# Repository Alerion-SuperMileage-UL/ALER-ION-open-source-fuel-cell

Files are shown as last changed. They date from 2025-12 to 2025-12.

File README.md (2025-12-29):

# ALÉR-ION OPEN SOURCE HYDROGEN FUEL CELL
*Feel free to contact me at mederic.chalifour.1@ulaval.ca for any questions.*

Alérion Supermileage is a student group at l'Université Laval who focuses on the development of high efficiency vehicles for various competitions. Up until 2024, the team always relied on internal combustion engines. They then transitioned toward an electric-driven system with a battery. In 2025, the project of a self-made hydrogen PEM fuel cell was born. With the spirit of sharing knowledge and helping others develop this technology, all the relevant design files are released as an open-source project.

This is a PEM open cathode fuel cell which turns pure (or prehumidified) hydrogen gas into electrical power.

**DISCLAIMER: At the moment of writing this, the prototype still has reliability issues. This stack is prone to leaking. Alérion Supermileage and every contributors of this project waive all responsibility related to the usage of this fuel cell design. Note that hydrogen is a flammable gas. Use these files at your own risk.**

{F411903D-C956-4F15-B26A-56FD519BAC25}



# Stack general design
This project was realized as a "Projet de fin d'étude" and the final design report is available (in French) in [Additional documentation/Rapport_final_PFE.pdf](https://github.com/Alerion-SuperMileage-UL/ALER-ION-open-source-fuel-cell/blob/f2cdef219edfe725619d7147de9b8b1a14c1f4f9/Additional%20documentation/Rapport_final_PFE.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). 

The aimed power rating of this fuel cell is ~300 W. Some PEM fuel cells can reach a power density of 0.6 W/cm², so the total active surface area needs to be at least 500 cm². Next, the maximum voltage allowed in this project was 60V. With the assumption that the maximum voltage per cell, would be ~1 V in operation, the stack would require ~60 cells of 8.3 cm² of active area. This figure was rounded up to a square of 3 cm × 3 cm (9 cm²) to optimize the cutting of the 30cm x 30cm electrode sheets. Note that the 60 cells can be distributed in more than one stack connected in series to facilitate the assembly and maintenance.

# CAD files
The CAD files for this project are available in [CAD files](https://github.com/Alerion-SuperMileage-UL/ALER-ION-open-source-fuel-cell/tree/main/CAD%20files). All files are available in *.step* format and as fusion 360 files (with the history tree for easy modification).

The `Fuel cell stack assembly` file is the CAD file of the whole fuel cell stack.

# Bill of materials
The bill of materials is available in [BOM/BOM.xlsx](https://github.com/Alerion-SuperMileage-UL/ALER-ION-open-source-fuel-cell/tree/main/BOM).

# Membrane Electrode Assembly (MEA)

The MEA is composed of two carbon cloth electrodes sandwiched around a proton-exchange membrane.

{682CDC34-29BD-45FB-BDDA-95B5D1C561A5}

  ## Proton exchange membrane
  The proton exchange membrane used was a [HP9-Pt ePTFE Reinforced, Pt Impregnated PFSA Membrane](https://www.fuelcellstore.com/eptfe-reinforced-pfsa-membrane-9-microns-pt-impregnated?search=78010010) from the [Fuel Cell store](www.fuelcellstore.com).

**Note:** 

* The membrane is shipped with a plastic cover film on one side. This film is useful to hold the membrane flat during the cutting and hot pressing steps, but should be removed before the stack assembly.
* Being only 9 µm thick, this membrane was selected aiming for high performance. However, even though it could handle the working pressure (~6 psi) when tested in a single cell stack, it was shown to be a weak point when scaling up to multiple cells. It seems to be easily punctured or torn, either in the manual assembly process or by the hydrogen pressure.
* " [...] *This membrane has a cover film on one face in order to protect the membrane during shipping.  Platinum impregnation is done on the face that is away from the cover film. For best utilization of the Pt impregnation from the membrane manufacturer, it is recommended that the Pt side is placed toward the anode of the electrolyzer cell (cathode of the fuel cell) electrochemical cell.  This Pt impregnation is actually a Pt nanopowder that is incorporated into the entire surface of the membrane on the side opposite the single backing.  This platinum layer is not sufficient to sustain the electrochemical reactions of the cells, it is only intended to react the minute crossover gases that occur naturally in all membranes.* [...]" 

**Recommendation:** For future development, it might be wiser to start using a thickness closer to the industry standard of 50 µm to obtain a reliable stack, and then go down in thickness to optimise the performance.

  ### Automated cutting
  In order to cut each membrane precisely and reliably, an *Ender 3* 3D printer was converted to a CNC drag knife using a "plotter blade". During this process, the membrane was left on its protective plastic film.

**Close up picture of the cutting process:**



### Membrane CAD file
The CAD file for the membrane can be found in [CAD files/Membrane](https://github.com/Alerion-SuperMileage-UL/ALER-ION-open-source-fuel-cell/tree/main/CAD%20files/Membrane).

  ## Electrode

The electrode selected for this project was the [2 mg/cm² Platinum Black - Carbon Cloth Electrode (W1S1011)](https://www.fuelcellstore.com/carbon-cloth-2-ptb-gas-diffusion-electrode-w1s1011?search=11060067) from the [Fuel Cell store](www.fuelcellstore.com). They were cut in 30mm X 30mm using a utility knife.

**Note and recommendation:** A high platinum loading of 2 mg/cm² was selected aiming for high performance. This choice inflates the cost of the stack by a lot and a lower platinum loading (0.5 mg/cm² for example) could be used to reduce the testing and development cost. Also note that the carbon cloth electrode, which was selected for being easier to work with compared to carbon paper electrode, is better suited at high humidity level [(Wang, 2007)](https://doi.org/10.1016/j.electacta.2006.11.012).

  ## Hot press
To make each MEA, the precut membrane is hot pressed between two precut electrodes. The heated press used in this project is a *5 Ton Portable Hydraulic Heat Press Machine 2.3 x 4.7 Inch*.



For each MEA, a printed template and some tape were used to align the electrode to the membrane. The membrane was left on its plastic protective film during the pressing but the bottom electrode was inserted between the membrane and the film by lifting the corner with some tweezers (beware not to scratch the membrane). Note that the platinum coating of the electrodes must face the membrane. 

Each MEA was hot pressed at 66 kg/cm², 97°C for 3.56 minutes to optimize the stack's performances [(Okur, 2013)](https://doi.org/https://doi.org/10.1016/j.energy.2013.05.001). The pressure was set suspending a weight on the press lever (accounting for the hydraulic mechanical advantage) and considering the area of the electrodes only (9 cm²).

# Graphite flow plates
The flow plates (bipolar plates), were made of 0.125" thick [Fully Resin Impregnated Graphite Plates](https://www.fuelcellstore.com/impervious-bipolar-graphite-plates). 
  ## Machining
  Each Plate were manufactured using a small benchtop CNC router (_Genmitsu CNC 3018-PRO_) with a 1/32" endmill.

**Note:** 
* Machining graphite produces a very fine dust. This should be done in a well ventilated area with appropriate respirators. A shop-vac was used to further control the produced dust.

  ## Flow field design and geometry
    Multiple flow fields geometry were tried and the ones producing the most power were selected. However, it should be noted that there was a high degree of uncertainty on the results so this process should be done again in the future.
    ### Hydrogen side (anode)
  Among others, the following flow fields were tried on the anode side:

IMG_5936 (1)

  The simple serpentine flow field was selected.
  
{30DB0875-6CFB-4B4F-8EC1-B9351816C968}

### Air side (cathode)

  All cathode flow fields that were tried followed the same idea of straight channels. The selection process was done before the optimisation of the gasket system. Indeed, nickel strips were added as back support for the gasket. The initial design was thus one that allowed the first PTFE gasket to self support and wasn't necessarily the most efficient one.

  {ACC28917-BCA8-4B8C-A650-7DEC884F8421}

  **Note:** 
  * The cathode design should be a balance between the conductivity (more graphite in contact with the electrode) and air availability (less graphite in contact with the electrode)
  * The depth of the channels also affects the strength of the plates. This should also be considered as cracked plates cause leakage.
### Other features
  #### O-ring slots
  The first design of the sealing system included o-rings on both sides of the bipolar plates. These are no longer in the design as its sealing ability was highly sensitive to the o-ring grooves depth, causing reliability issue. The same plates were later retrofitted to work with flat gaskets. The cathode side o-ring grooves were filled using silicone and some custom 3D printed spacers. The cathode side o-ring grooves can thus be removed from later version without any trouble (probably...). The anode side groove is also not used anymore, further tests should be conducted before removing it from the design as the gasket system was designed to fit on plate with this feature. If removed, one possible risk could be that the current EPDM gasket which had this space to be squished-in before (thus not geting out of the PTFE subgasket), could reach the membrane and damage it. 
  
***New design still shouldn't include this feature, but careful consideration must be taken if the gasket system remains unchanged.***

{8F8FE4D9-8604-4AC9-B960-A8A56247C3E5}

  #### Holes
  Each flow plates has four holes: two port (inlet and outlet) and two other for the positioning rods.
  ### End flow plates
  The end flow plates must be different to allow contact with the current collectors without causing any leaks. For the cathode side of the stack, the last flow plate didn't have the inlet/outlet holes and the anode side of the plate was left uncarved. This allowed maximal contact with the current collector while elimating the need for a sealing system around the ports.

  For the anode side of the stack, where the inlet and outlet are, the o-ring grooves of the cathode side of the plate were not filled like the other plates. At least for this last plate, the o-ring grooves needs to stay in the design. Moreover, although it's not necessary, the cathode side flow fields can be removed to allow maximum contact with the current collector.
  ## CAD file
The cad files of the flow plates can be found in [CAD files/Flow plate](https://github.com/Alerion-SuperMileage-UL/ALER-ION-open-source-fuel-cell/tree/main/CAD%20files/Flow%20plate).

# Sealing and gaskets 
Sealing the fuel cell turned out to be an unforeseen major challenge of this project. During this process, multiple iterations of the gasketing system were tried and a procedure to test out the performance was developed. This section presents this procedure, along with the final design of this system.

sealing diagram

## CAD file
The CAD for the sealing system can be found in [CAD files/Sealing system](https://github.com/Alerion-SuperMileage-UL/ALER-ION-open-source-fuel-cell/tree/main/CAD%20files/Sealing%20system).

## Testing procedure
Each new gasket system needed to pass 3 distinct tests.
### Electrical contact
First, the gasket shouldn't affect the electrical performance of the fuel cell. In other words, we had to ensure that the electrical resistance between the carbon clothe electrodes and the graphite bipolar plates didn't increase when the gasket was added. This meant that the gaskets, once compressed, shouldn't be thicker than the electrodes. To test this, we used a stack of two bipolar plates with the current collectors and sandwiched only one electrode, without the membrane and the gasket to measure the resistance. The voltage drop was measured with constant current power supply of 5 A applied on the current collectors. This baseline resistance was on the order of 9mOhm. Then the same experiment was repeated with the gasket system (half of it if it was symmetrical, else two stacked electrode are required). The resulting resistance had to be in the same range. This test was also used to determine the effect of different torque on the compression screws on the cell resistance.
### Membrane integrity
During the testing phase, we observed that some gasket systems would damage the proton exchange membrane. In other words, squishy materials, like EPDM rubber, would grip on the membrane and stretch it out, causing small tears which majorly compromised the sealing structure. This observation led to the introduction of a thin PTFE sub-gasket in the design. When we tested different system, instead of testing with a new MEA each time, we would try with a simple humidified membrane and then observe it directly (the membrane shouldn't be deformed or damage by compressing it in the fuel cell).
### Leak test
The final test for the fuel cell was a submerged leak test. For this test, some compressed air was used to see if the fuel cell would hold the design pressure (6-10 psi). Note that it was simpler and safer to use air from the workshop than to go in the lab to try this with hydrogen. Then, the fuel cell was submerged in distilled water in a transparent pot to identify the origin of the leaks (or to find smaller ones). Each new design was first tested with only one or two cells, and later retested with more and more cells to validate the sealing system.

## Main gasket
The last iteration of the main gasket was cut out of a [15 mil EPDM 50A rubber sheet](https://www.grainger.ca/en/product/p/WWG2UNW5). It was cut using the same procedure as the proton-exchange membrane, with double sided tape (from Dollarama) to hold it to the 3D printer bed. This procedure was far from perfect as the rubber tends to be dragged up by the cutting blade. Multiple slow passes were made to alleviate this issue, but the fail rate was still high. A real CNC drag knife with a longer cutting blade, or laser cutting might help.

For further iteration, harder rubber (EPDM 70A) should be tried as it would probably be easier to cut, and it might hold pressure better. 

The benefit of this material, over teflon, which is way easier to cut-out, is that it compresses well, allowing a good electrical contact and a good seal at a reasonable compression (too much compression breaks the graphite). However, it also caused several issues. 

{1AAF5251-57B7-48D0-AB14-D3F54ACDE881}

## Subgasket
First, because of its "squishiness" and good gripping properties, when compressed, the EPDM gasket  would grip on the proton exchange membrane (PEM) and tear it as the contact surface would expand under compression. To solve this, a 1 mil PTFE sub-gasket was added (this feature is known as edge protection [(Min Wang et al 2019)](https://iopscience.iop.org/article/10.1149/09208.0351ecst)). This created a slippery protective layer between the PEM and the EPDM gasket, without compromising the seal. It was cut out using the same procedure as the PEM and the EPDM gasket. For further improvements, 2 mil PTFE subgasket could be tried to improve the durability of this piece, as it tends to wear out after being compressed.

{ACD0C022-2CFB-4C2A-B5AC-9CDCB83F5C3C}

## Back support and margins
Next, because of its high compressibility, the EPDM gasket tended to squish in the hydrogen channels, cutting out the hydrogen flow entirely. Nickel back support were thus added where the gasket had to go over the flow channels. Also, appropriate margin between the gasket holes and any flow field feature (flow channels, port holes, etc.) were needed has the gasket expands under compression. To spot where to add more margin, we looked at the marks left of the rubber after the compression.

The nickel back support were made with 0.1mm x 4mm 99.6% pure nickel strip, which was cut to the desired length. **Be sure to use pure nickel as nickel plated steel will rust.**

These nickel strips were held in place using a small amount of silicone. For further improvements, some feature in the graphite flow plates should be added to accurately position the back support strips.

## Sealing interface with negative current collector and end plate
The first and last flow plates are special cases in regard to sealing. For the last flow plate (the first one being the closest one to the ports), the inlet and outlet holes were simply omitted, which naturally keeps the hydrogen from reaching the current collector.

For the first plate, a sealing solution that keeps an electrical contact between the collector and the first flow flow plate is required. A simple gasket wouldn't work here as it would cut the electrical contact (unless it's conductive). The seal was thus realized by o-rings (dash number 010, 1/16 fractional width). Ideally, there would have been one o-ring per port, and a groove on the flow plate on the side facing foward the current collector. However, from previous iteration of the sealing system, the other side of the flow plate already had an oring groove (filled with silicone and plastic for the rest of the stack). This situation had us bore the oring groove all the way accross the plate, and using two oring stacked toghter with a piece of PTFE btween them. That's far from optimal and should be changed in the next iteration.

{D819177F-0591-4949-9D88-9786E186D766}

To seal off the interface between the first current collector and the first end plate, a simple gasket, made from the same material as the main gasket was used.

{8BC15475-6748-409D-AFD8-CBDC90FAE1FF}

# Current collectors
The current collectors act as the electrical interface between the fuel cell stack and the electrical circuit. Copper was selected for its high electrical conductivity, but surface corrosion was a concern. To prevent it, the current collectors were silver coated using [Nushine Silver Plating Solution 3.4 Oz](https://a.co/d/675oinK).

IMG_5931 (1)
{44C0C773-2CE3-48D9-A187-1A2DAB118852}

Originally, a 0.1mm thick pure copper sheet was used, but it was replaced by double sided copper laminated FR4 (blank PCB material), after the first iteration got damaged. In the end both solutions weren't optimal and a thicker pure copper sheet may perform better.

The electrical circuit was connected to the collectors using simple fork terminals bolted on the tabs.

## CAD files
The CAD files for the current collectors can be found in [CAD files/Current collectors](https://github.com/Alerion-SuperMileage-UL/ALER-ION-open-source-fuel-cell/tree/main/CAD%20files/Current%20collectors).

# End Plates
{9884F5E0-8846-489C-B124-512537534B9E}

## Material
In order to have a reliable seal and a well distributed compression, the end plates need to be very stiff. To achieve this while keeping a light weight, the selected material was a 3/8" thick [Flame-Retardant Garolite G-10/FR4 Sheet](https://www.mcmaster.com/85345K752/). Note that this material is very abrasive and might damage the tooling bits. 
## Ports
The selected connectors were [Swagelok's #SS-400-1-0256](https://products.swagelok.com/en/c/straights/p/SS-400-1-0256). A 10-32 thread was tapped directly in the garolite sheets.

To keep the fitting tight over time, threadlocker was added and along with a 3D printed contraption that prevents the rotation of the two fittings, like a lock wire.

## Compression
To compress the stack, eight M4 threaded rods were used to compress the two end plates together. A nut was also welded on one end of each rod to turn it into a long hex head bolt. [High profile nuts](https://www.mcmaster.com/90725A025/) were used to avoid stripping. Also note that [washers](https://www.mcmaster.com/93475A230/) are needed to avoid damage on the end plates during compression. 

## CAD files
The CAD files for the endplates can be found in [CAD files/Endplate](https://github.com/Alerion-SuperMileage-UL/ALER-ION-open-source-fuel-cell/tree/main/CAD%20files/Endplate).

# Air blower
The first tests of the fuel cell stack indicated that the current was limited by the low air flow in the flow field. This could be due to oxygen concentration or water removal.

A **PVB120G12H-P01** air blower, scavenged from an old computer was installed along with a 3D printed duct to guide the air through. This blower can accommodate for about 20 cells. The exact geometry of the duct can also be modified to fit the length of the stack.

A filter was also crafted with a 3D printed frame and a piece composite breather material to avoid any contaminant in the air supply of the fuel cell stack.

{8FADFDFD-DADD-46EE-878C-21586577273D}

## CAD files for the duct and filter
The CAD files for the air blower system can be found in [CAD files/Air blower system](https://github.com/Alerion-SuperMileage-UL/ALER-ION-open-source-fuel-cell/tree/main/CAD%20files/Air%20blower%20system).

# Stack assembly procedure

An extensive assembly procedure was never put together. However, here are a few guidelines for the assembly:

* First, the MEAs must be pre-humidified before being put in the stack. To do so, the MEAs are left to float in distilled water  for a few minutes. Wetting the gaskets and sub-gaskets can also help.
* When handling the MEA, wear clean gloves to avoid contaminating the membrane with any grease.
* To assemble the MEA with the gasket and flow plates, start using the end plate with the positionig rods. Each element is then slide through on top of each other.
* Beware not to leave any folds or wrinkle in the MEA and gaskets.
* Make sure that the membrane is protected from the main gasket by the sub-gasket. Any contact between the two during compression will lead to tear in the membrane.
* To compress the stack, use a torque screw driver. All eight threaded rods must be bolted in a star pattern with multiple increments in the torque. The final value of the torque is 75 Ncm. This value can be adjusted, but beware: more torque can lead to some cracks in the flow plates, and less torque can lead to leaks in the stack.
* A set of 3D printed screwdriver wrench were used for this project. This worked well, but I would recommend to buy this tool for a better repeatability.
* About half-way through the compression, when the risk of movements between the cells is low, remove the positioning rods.
* For the O-rings, Swagelok fitting (with a rubber gasket) and endplate gasket, a bit of silicone grease can be added to help the gasket to create a good seal. **Note that this must NOT be done on the main gasket, or any component in contact with the membranes, because it can damage them.**
* The maximum recommended number of cells per stack is ~20.

## Positioning rods
In order to facilitate the allignement of everything during the assembly, two [4 mm OD fiber glass rods](https://a.co/d/973gxrt) were included in the design. Each part has two 4 mm hole (+ tolerance) to let the positioning rods go through. 

About mid way into the compression of the stack, when the risk of shifting of the components is reduced, the rods are removed to remove all friction that could result in uneven compression across all cells.

# Performances
## Testing
The full fuel cell stack has not been tested yet. However here is a preliminary result for a single cell. The jump in the curve is likely due to a bad caracterisation of the resistive load. 

polariz2 (1)

This early results shows that the achieved power density is around 0.13 W/cm², which is short from the 0.6 W/cm² target. A lot of factors may cause this performance loss. First, a bad contact between the electrodes and the flow plates might be the cause. Note that this test was performs with another gasket design, and that the current gaskets supposedly help with the electrical contact. 

Next, the temperature and humidity of the cell, for this test, were neither measured, nor controlled. The operating conditions were therefore not optimized for the performance.

Finally, it is possible that the air supply was insufficient, making the oxygen the limiting factor in the reaction. Note that this early test was performed with another fan/blower than the one presented in this design.

# Acknowledgement
Huge thanks to all our sponsors and to all the experts who helped us along the way!

github-1

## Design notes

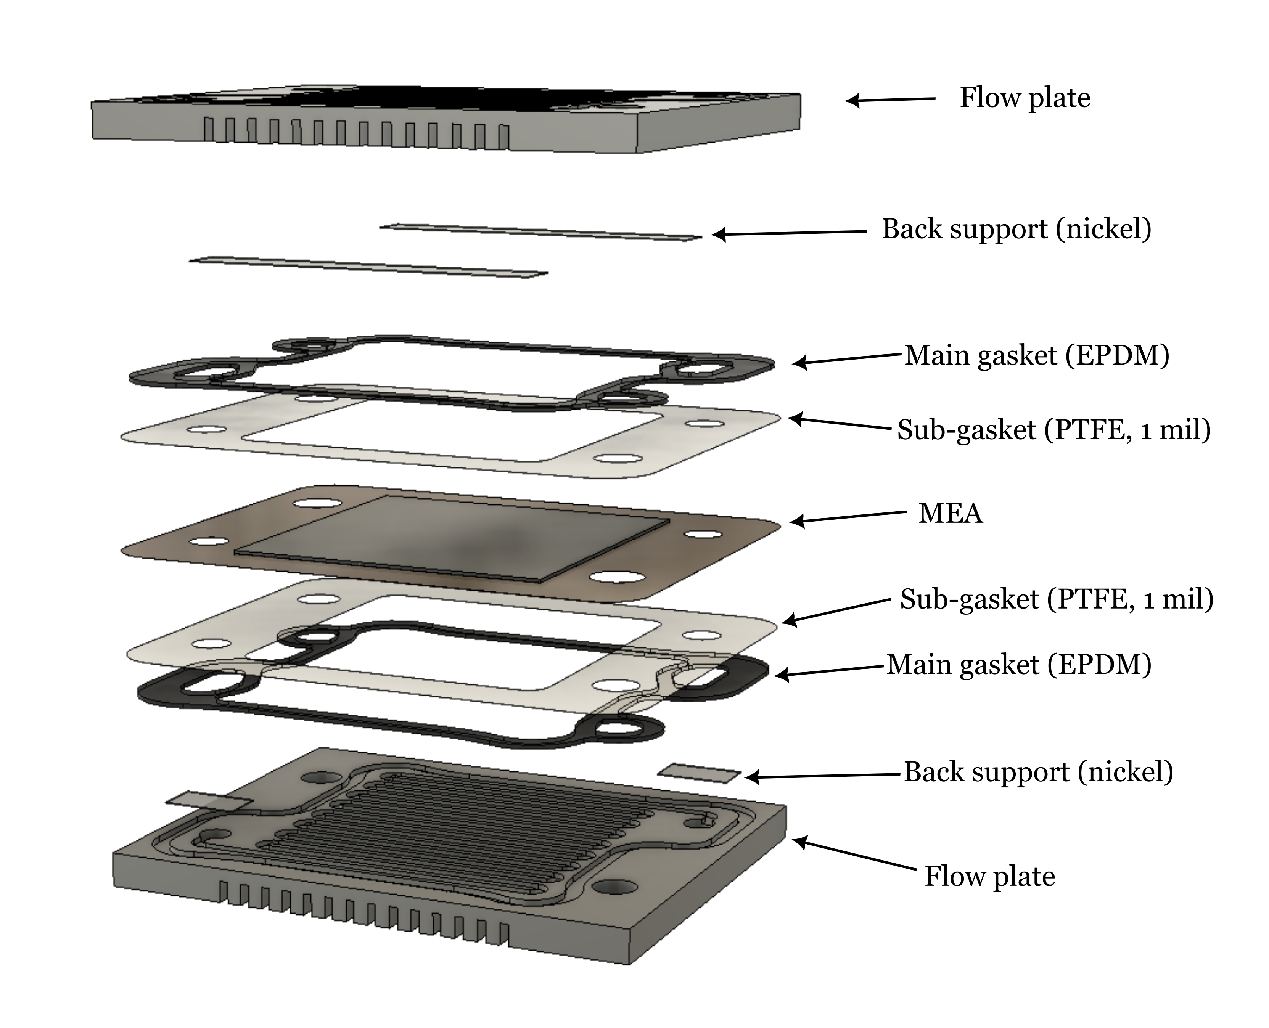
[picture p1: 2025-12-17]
CAD files/Sealing system/sealing diagram.png

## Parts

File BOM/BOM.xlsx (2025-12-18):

Bill of materials
Function | Description | From | Part number | Note | Link
Swagelok ports | Stainless Steel Swagelok Tube Fitting, Male Connector, 1/4 in. Tube OD x #10-32 Male Thread | Swagelok | SS-400-1-0256 |  | https://products.swagelok.com/en/c/straights/p/SS-400-1-0256
PEM | HP9-Pt ePTFE Reinforced, Pt Impregnated PFSA Membrane | The Fuel Cell Store | 78010010 | Use a thicker membrane for next iteration | https://www.fuelcellstore.com/eptfe-reinforced-pfsa-membrane-9-microns-pt-impregnated?search=78010010
Electrode | 2 mg/cm² Platinum Black - Carbon Cloth Electrode (W1S1011) | The Fuel Cell Store | 11060064 | 0.5mg/cm2 might be sufficient | https://www.fuelcellstore.com/carbon-cloth-2-ptb-gas-diffusion-electrode-w1s1011?search=11060067
Flow plate | Fully Resin Impregnated Graphite Plates | The Fuel Cell Store | 42090001 |  | https://www.fuelcellstore.com/impervious-bipolar-graphite-plates
Main gasket | RUBBER SHEET, MILITARY, 12 IN X 36 IN, 0.01563 IN THICK, 50A, PLAIN BACKING, BLACK, SMOOTH | Grainger | WWG2UNW5 | Maybe use use harder rubber (70A ?) | https://www.grainger.ca/en/product/p/WWG2UNW5
End plate | Flame-Retardant Garolite G-10/FR4 Sheet Multipurpose, 6" x 6", 3/8" Thick | McMaster-Carr | 85345K752 |  | https://www.mcmaster.com/85345K752/
Nuts for compression | Zinc-Plated Steel High-Profile Hex Nut, Class 6, M4 x 0.7 mm Thread | McMaster-Carr | 90725A025 | Wing nuts also work | https://www.mcmaster.com/90725A025/
Washer for compression | 18-8 Stainless Steel General Purpose Washer, for M4 Screw Size, 4.3 mm ID, 9 mm OD | McMaster-Carr | 93475A230 |  | https://www.mcmaster.com/93475A230/
Nickel back support | HARFINGTON Pure Nickel Strip 0.1mm x 4mm 32.8ft 99.6% Nickel Solid Pure Nickel Strips for Lithium Battery Packs Car Nickel Solder Tap for Cell Battery Pack Spot Welding and Soldering | Amazon |  | Make sure to order PURE nickel, not steel plated nickel!! | no longer available
Silver plating solution | Nushine Silver Plating Solution 3.4 Oz - permanently plate PURE SILVER onto worn silver, brass, copper and bronze (Ecofriendly formula) | Amazon |  |  | https://a.co/d/7pSMaic
Copper sheet (first current collector iteration) | Copper Flashing 99.95% Pure - 38 Gauge 0.1mm Thick Copper Strip - Solid Copper Roll in Various Widths & Length – ASTM B152M Copper Sheet - Contractors & DIY Projects (38 Ga, 2" Width x 3.5 FT) | Amazon |  | Use thicker copper sheet | https://a.co/d/dvtPuwn
Blank PCB material | uxcell Double-Sided Copper Clad Laminate PCB Circuit Board, FR4 180x120mm 7.09x4.72 inch, 1.5mm Thickness DIY Prototyping PCB Board, Name Board, 5pcs | Amazon |  | Use thicker copper sheet instead | https://a.co/d/4i2m5fk
Positioning rods | 10pcs 500mm Fiberglass Rodding, Glass Fiber Round Bar, 2-10mm Dia High Strength Fiberglass Solid Rod for Making Kites | Amazon |  |  | https://a.co/d/2Bn6HCn
Air blower | Air nlower from an old computer |  | PVB120G12H-P01
Threaded rod for compression | M4 threaded rod
O-ring | o-ring, dash number 010, 1/16 fractional width
Sub-gasket | PTFE film, 0.001" thick |  |  | Maybe try a 0.002" thick one

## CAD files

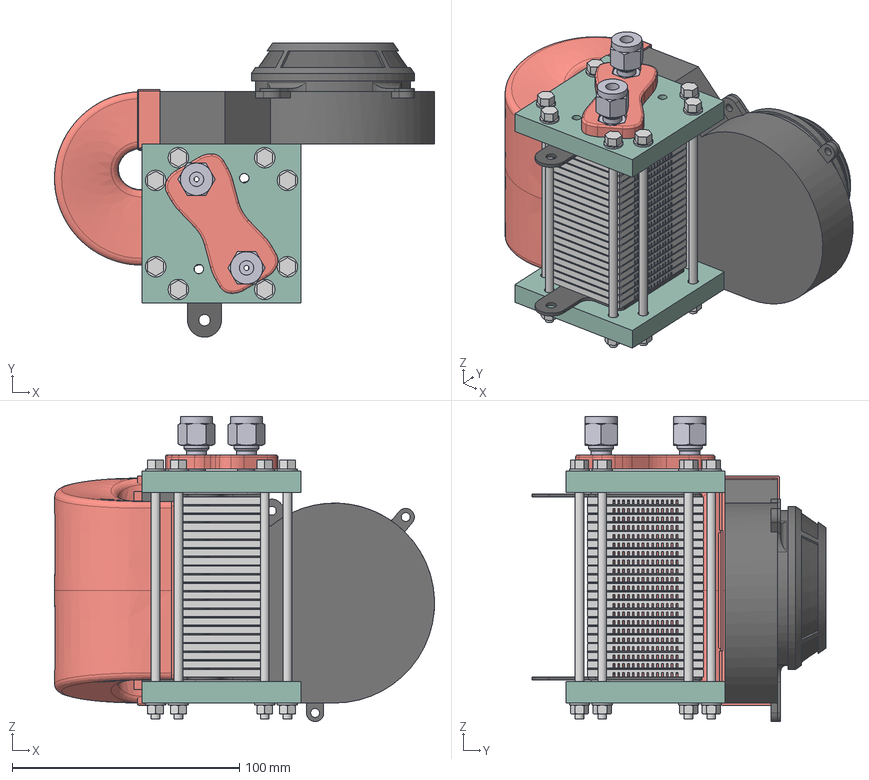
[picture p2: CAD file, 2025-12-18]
CAD files/Fuel cell stack assembly.step
167.2 x 129.6 x 134.3 mm
Endplate
PRODUCT_ID_1 x 2
current collector
gasket end
fitting locker
G Paramétrique v52
gasket v2 x 40
Membrane x 20
G Paramétrique v52 (3) x 20
electrode x 40
Sub-gasket (PTFE) x 40
Back support hydrogen x 20
Back support air x 20
3d filler x 40
Endplate(Symétrie miroir)
current collector(Symétrie miroir)
gasket end(Symétrie miroir)
Fan - PVB120G12H-P01
filtre base
filtre cap
Composant4
duct en U
tige fileté x 8
93475A230_18-8 Stainless Steel Washer x 16
90725A025_Zinc-Plated Steel High Hex Nut x 8
Squished O-ring x 2
ptfe oring spacer x 2

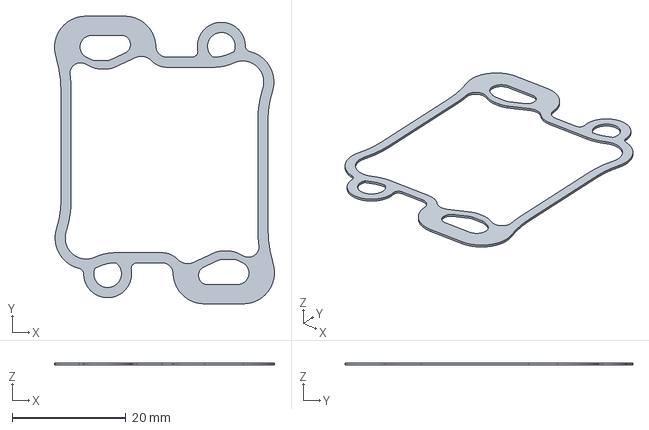
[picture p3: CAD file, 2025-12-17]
CAD files/Sealing system/Main gasket.step
38.7 x 50.6 x 0.381 mm

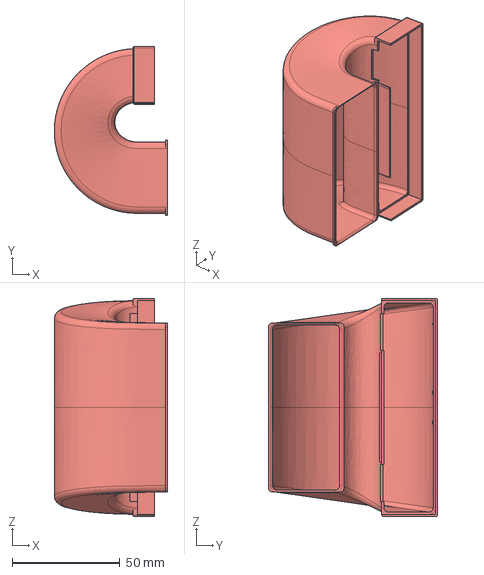
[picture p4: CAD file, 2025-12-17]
CAD files/Air blower system/Duct/duct en U v5.step
52.5 x 78.4 x 101.0 mm

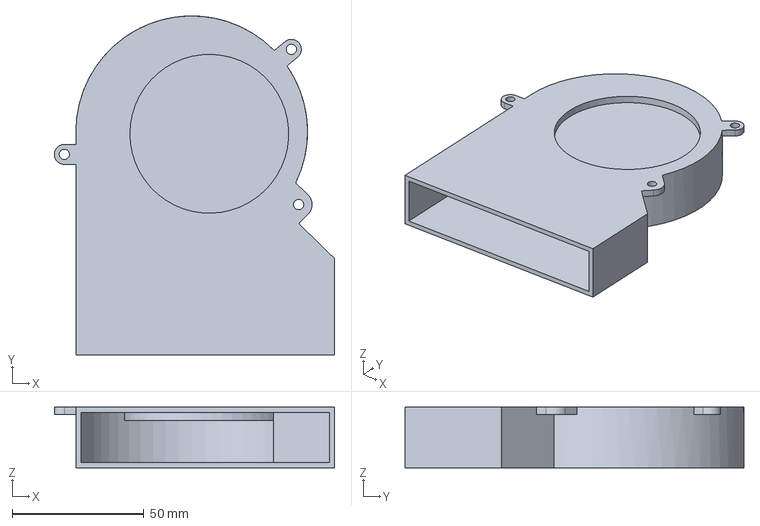
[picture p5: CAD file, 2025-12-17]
CAD files/Air blower system/Fan/Fan - PVB120G12H-P01 v4.step
106.5 x 128.7 x 23.1 mm

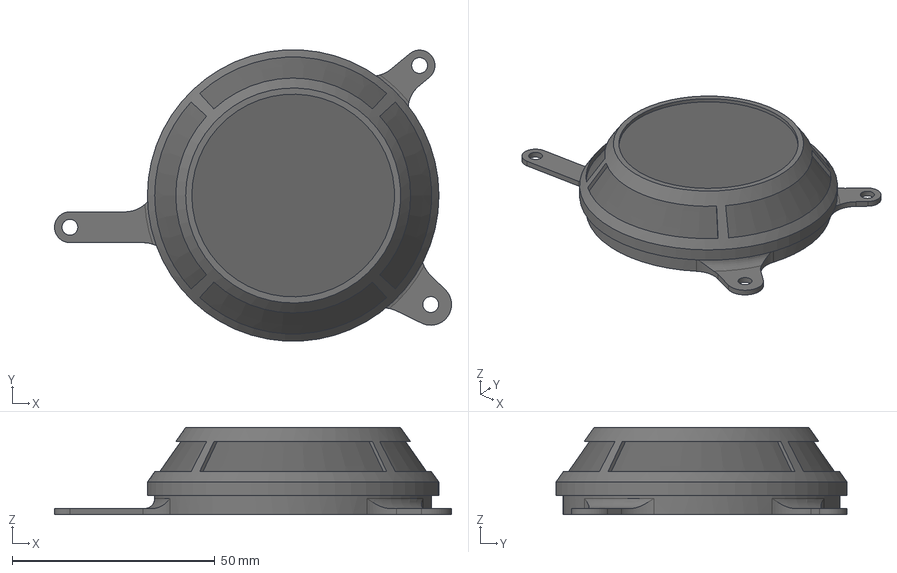
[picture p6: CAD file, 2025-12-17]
CAD files/Air blower system/Filter/filtre à air v10.step
97.9 x 71.8 x 21.5 mm
filtre base
filtre cap
Composant4

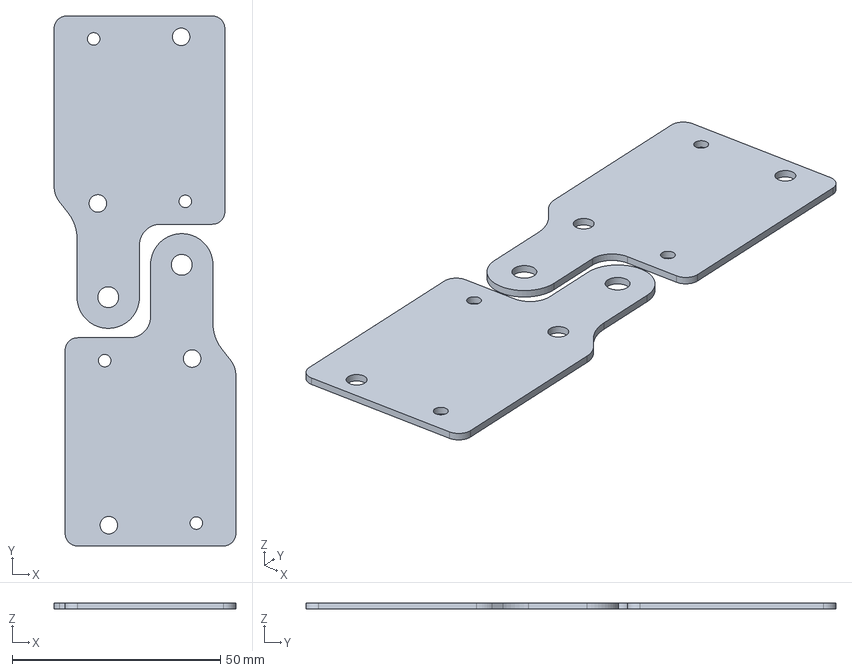
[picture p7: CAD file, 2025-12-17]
CAD files/Current collectors/Current collectors.step
43.6 x 127.2 x 1.50 mm

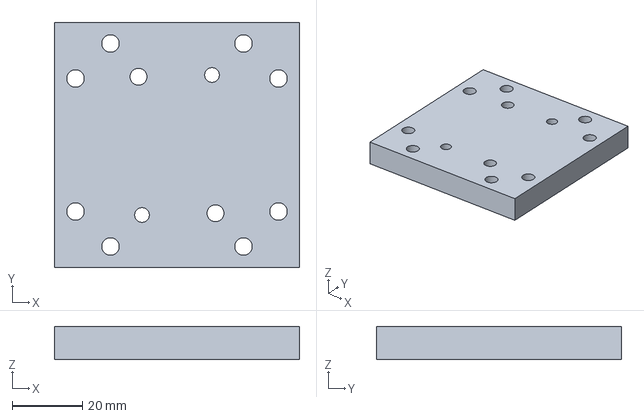
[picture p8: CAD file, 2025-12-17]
CAD files/Endplate/Endplate.step
70.0 x 70.0 x 9.52 mm

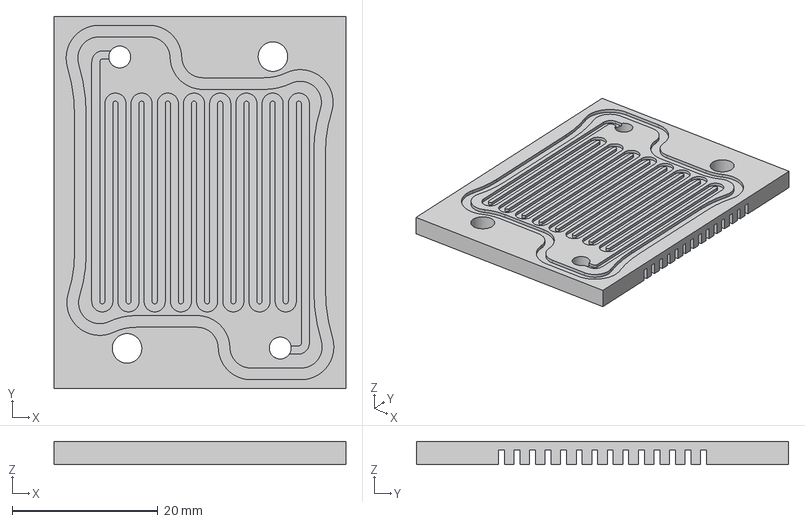
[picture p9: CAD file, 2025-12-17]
CAD files/Flow plate/Flow plate.step
40.0 x 51.0 x 3.18 mm

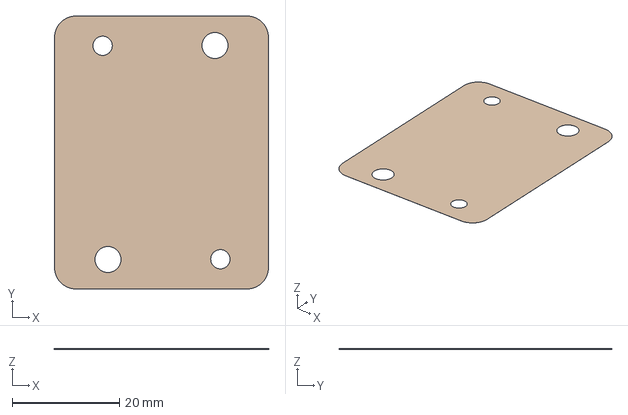
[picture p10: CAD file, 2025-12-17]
CAD files/Membrane/Membrane.step
40.0 x 51.0 x 0.01 mm

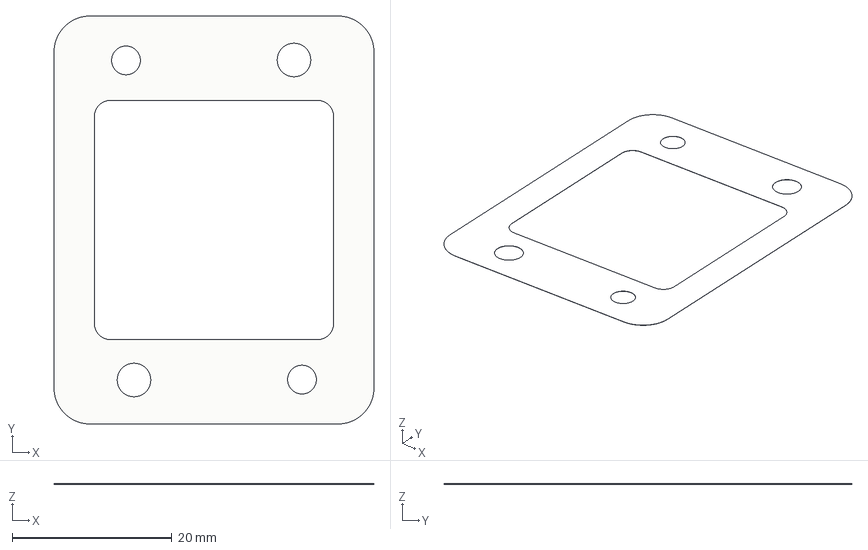
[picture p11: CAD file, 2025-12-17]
CAD files/Sealing system/Sub-gasket.step
40.0 x 51.0 x 0.0254 mm

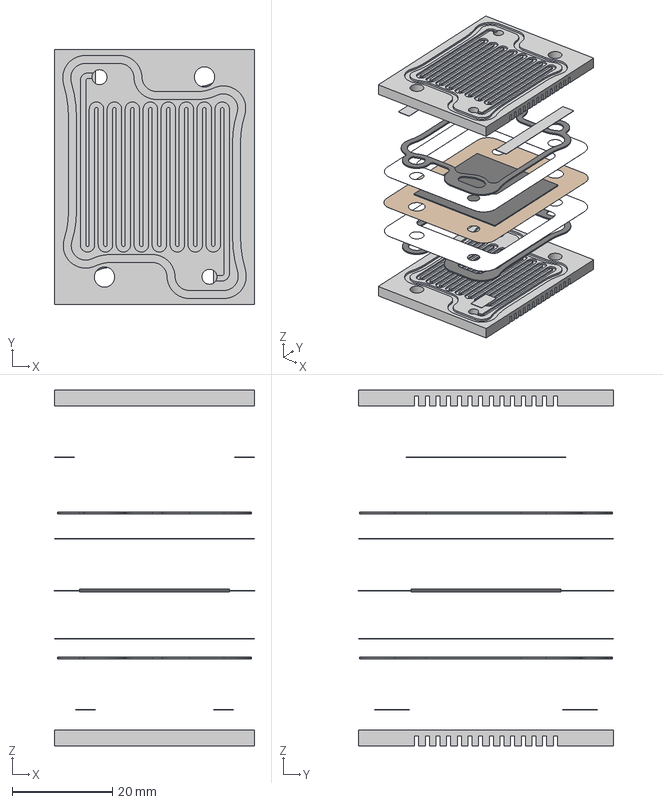
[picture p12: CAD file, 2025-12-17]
CAD files/Sealing system/nouveaux gasket qui va marcher v74.step
40.0 x 51.0 x 71.2 mm
G Paramétrique v51
gasket v2 x 2
PTFE film x 2
h2
air
G Paramétrique v51_1
Membrane
Électrode x 2

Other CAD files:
CAD files/Air blower system/Duct/duct en U v5.f3d
CAD files/Air blower system/Fan/Fan - PVB120G12H-P01 v4.f3d
CAD files/Air blower system/Filter/filtre à air v10.f3d
CAD files/Endplate/endplate v3.f3z
CAD files/Flow plate/G Paramétrique.f3z
CAD files/Fuel cell stack assembly.f3z
CAD files/Membrane/Membrane qui va marcher.f3z
CAD files/Sealing system/nouveaux gasket qui va marcher.f3z

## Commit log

2025-09-27 Enhance README with MEA details and cutting process
    Updated section titles and added details about the Membrane Electrode Assembly and automated cutting process.
2025-09-27 Update README with Bill of Material and CAD files
    Added a section for Bill of Material and marked CAD files as TODO.
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2025-09-29 Fix wording in README about flow plate design
2025-09-29 Revise gasket and current collector sections in README
    Restructured sections related to gaskets and current collectors in the README.
2025-11-02 Revise gasket section and testing procedures in README
    Updated the README to clarify gasket materials and testing procedures, including the introduction of a PTFE sub-gasket to prevent membrane damage. Added details on the manufacturing process of the main gasket and back support.
2025-11-02 Update README with CAD file section and testing procedures
    Added a section for CAD file and outlined testing procedures for gasket systems, including electrical contact tests.
2025-12-17 Update README with material and connector information
    Added details about material properties and selected connectors.
2025-12-17 Update compression section in README
    Clarified compression method using M4 threaded rods and nuts.
2025-12-17 Update README with design details and corrections
    Refactored sections on cathode design, sealing system, and end flow plates for clarity and consistency. Added images and corrected minor typos.
2025-12-17 Enhance README with updates on sealing and collectors
    Updated the sealing interface section and clarified the role of current collectors. Added images and improved descriptions for better understanding.
2025-12-17 Fix image tags and update current collectors section
    Updated image tags and corrected text regarding current collectors.
2025-12-17 Enhance README with positioning rods information
    Added details about the use of positioning rods in the assembly process.
2025-12-17 Enhance README with sealing interface information
    Added details about sealing interface for flow plates.
2025-12-17 Enhance sealing interface section in README
    Expanded explanation of the sealing solution for the first flow plate, detailing the use of o-rings and design considerations.
2025-12-17 Fix spelling and grammar in README.md
    Corrected spelling and grammatical errors in the O-ring slots section of the README.
2025-12-17 Remove CAD file section from README
    Removed placeholder for CAD file section in README.
2025-12-17 Add CAD files section to README
    Added a section for CAD files in the README.
2025-12-17 Add CAD files section to README
    Added section for CAD files related to the duct.
2025-12-17 membrane cad
    [Membrane.step]
2025-12-17 Add CAD file reference for membrane
    Added link to the CAD file for the membrane.
2025-12-17 Add Membrane STEP file for CAD representation
    [Membrane.step]
2025-12-17 Fix link format for membrane CAD file in README
2025-12-17 Implement feature X to enhance user experience and optimize performance
    [Membrane qui va marcher.f3z]
2025-12-17 Flow plate cad
    [Flow plate.step, G Paramétrique.f3z]
2025-12-17 Add link to CAD files for flow plates in README
    Updated the README to include a link to the CAD files for flow plates.
2025-12-17 CAD current collectors
    [Current collectors.step, endplate v3.f3z]
2025-12-17 Update CAD files section in README
    Added link to CAD files for current collectors.
2025-12-17 CAD endplate
    [Endplate.step, endplate v3.f3z]
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2025-12-17 CAD air blower
    [Fan - PVB120G12H-P01 v4.f3d, Fan - PVB120G12H-P01 v4.step, duct en U v5.f3d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]
2025-12-17 Revise CAD files section in README
    Updated section to include CAD files for the air blower system.
2025-12-17 CAD gasket
    [nouveaux gasket qui va marcher v74.step, nouveaux gasket qui va marcher.f3z]
2025-12-17 Add link to CAD files for sealing system
    Updated CAD file section with link to sealing system CAD files.
2025-12-17 CAD gaskets
    [Main gasket.step, Sub-gasket.step]
2025-12-17 CAD Whole fuel cell stack
    [Fuel cell stack assembly.f3z, Fuel cell stack assembly.step]
2025-12-17 Update CAD files section in README
    Added details about CAD files and their formats.
2025-12-17 remove bad cad
    [Fuel cell stack assembly.f3z, Fuel cell stack assembly.step]
2025-12-17 Clarify CAD file description in README
    Updated the description of the CAD files section.
2025-12-18 Enhance README with EPDM gasket insights
    Added details about EPDM gasket performance, sub-gasket implementation, and nickel back support to improve hydrogen flow and sealing.
2025-12-18 Add TODO for gasket between current collector and end plate
    Added a TODO note for a gasket between the current collector and end plate.
2025-12-18 CAD whole fuel cell.
    [Fuel cell stack assembly.f3z, Fuel cell stack assembly.step]
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2025-12-18 update cad
    [Fuel cell stack assembly.f3z, Fuel cell stack assembly.step]
2025-12-18 Fix Bill of materials section and add link
    Corrected the title from 'Bill of material' to 'Bill of materials' and added a link to the BOM.
2025-12-18 Restore stack assembly and positioning rods sections
    Restored the stack assembly procedure and positioning rods sections in the README.
2025-12-18 Update README with gasket information
    Added details about the gasket used between the first current collector and the first end plate, and removed the TODO note regarding the gasket.
2025-12-26 Enhance README with fuel cell design details
    Added details about the fuel cell's power rating and design specifications.
2025-12-26 Fix formatting of power density and area units in README
2025-12-26 Document assembly procedure for stack assembly
    Added detailed assembly guidelines for the stack procedure, including steps for handling the MEA, compression instructions, and recommendations for tools and materials.
2025-12-26 Clarify torque compression instructions
    Added a warning about torque adjustments affecting flow plates and leaks.
2025-12-26 Update README with preliminary fuel cell test results
    Added preliminary test results for a single fuel cell, including power density and factors affecting performance.
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
